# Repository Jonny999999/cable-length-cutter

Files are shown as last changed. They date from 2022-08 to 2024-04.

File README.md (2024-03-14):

# Overview
Firmware and documentation of a custom built machine that winds and cuts cable to certain lengths.  
Extensive details about this project can be found on the website: [pfusch.zone/cable-length-cutter](https://pfusch.zone/cable-length-cutter)

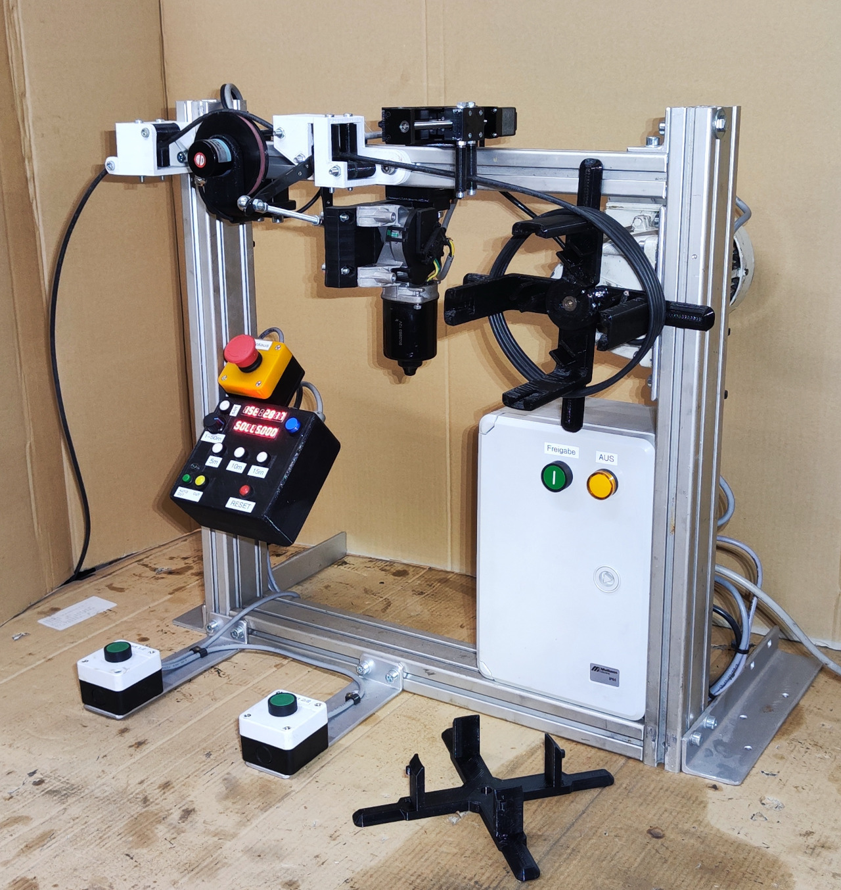
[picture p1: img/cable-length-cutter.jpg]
Photo machine


Photo of the built machine

## Current Features
- Measure length using rotary encoder
- Wind to set length while start-button is pressed
- Automatic wire cutter
- Control interface:
  - 2x 7-Segment display showing lengths and notifications
  - Buzzer for acoustic notifications
  - 4 Buttons and Potentiometer for setting the target length
  - Reset and Cut Button
- Stepper motor controlling a linear axis guiding the cable while winding
- Store last axis position at shutdown

# Usage
Panel Layout

# Electrical Details
For detailed documentation of all electrical aspects, see [connection-plan.pdf](connection-plan.pdf).

# Printed Parts
All designed and 3D-printed parts can be found in the [cad/](cad/) folder. These parts were designed using FreeCAD.

# Components
### Custom pcb with ESP-32 microcontroller
See [connection-plan.pdf](connection-plan.pdf)  

### Rotary encoder LPD3806-600BM-G5-24C
```
- Pulses: 600 p/r (Single-phase 600 pulses /R,Two phase 4 frequency doubling to 2400 pulses)
- Power source: DC5-24V
- Shaft: 6*13mm/0.23*0.51"
- Size: 38*35.5mm/1.49*1.39"
- Output :AB 2phase output rectangular orthogonal pulse circuit, the output for the NPN open collector output type
- Maximum mechanical speed: 5000 R / min
- Response frequency: 0-20KHz
- Cable length: 1.5 meter
- size: http://domoticx.com/wp-content/uploads/2020/05/LPD3806-afmetingen.jpg
- Wires: Green = A phase, white = B phase, red = Vcc power +, black = V0
```
### Variable Frequency Drive T13-400W-12-H
See [docs/vfd/](docs/vfd/)

### Stepper-driver TB6600
See [docs/stepper-driver_TB6600-Manual.pdf](docs/stepper-driver_TB6600-Manual.pdf)

### Linear Axis with Nema-12 28HB40 Stepper
See [connection-plan.pdf](connection-plan.pdf)  

# Installation
For this project **ESP-IDF v4.4.4** is required (with other versions it might not compile)
```bash
#download esp-idf
yay -S esp-idf 
#alternatively clone the esp-idf repository from github and do `git checkout release/4.4`

#run installation script in installed folder
/opt/esp-idf/install.sh
```

# Build
### Set up environment
```bash
source /opt/esp-idf/export.sh
```
(run once per terminal)

### Compile
```bash
cd board_single
idf.py build
```

# Flash
- connect FTDI programmer to board (VCC to VCC; TX to RX; RX to TX)
- press REST and BOOT button
- release RESET button (keep pressing boot)
- run flash command:
```bash
idf.py flash
```

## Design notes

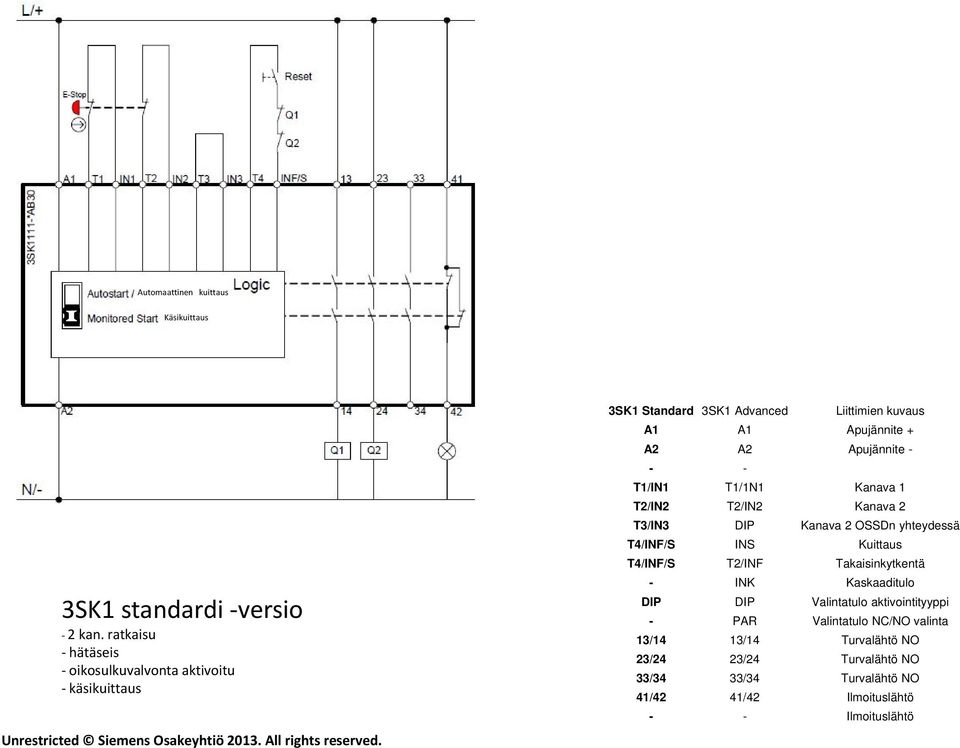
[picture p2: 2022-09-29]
docs/safety-relay_3SK1111-1AB30_con1.jpg

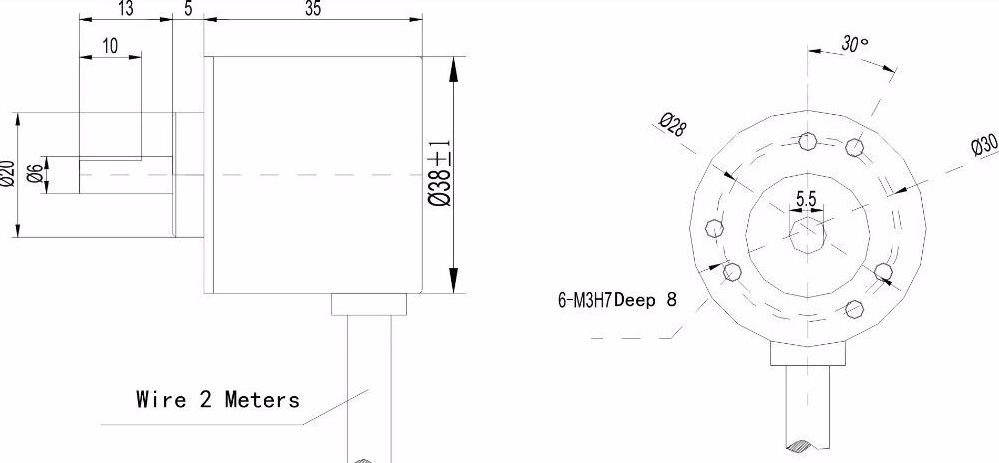
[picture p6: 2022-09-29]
docs/encoder-LPD3806_dimensions.jpg

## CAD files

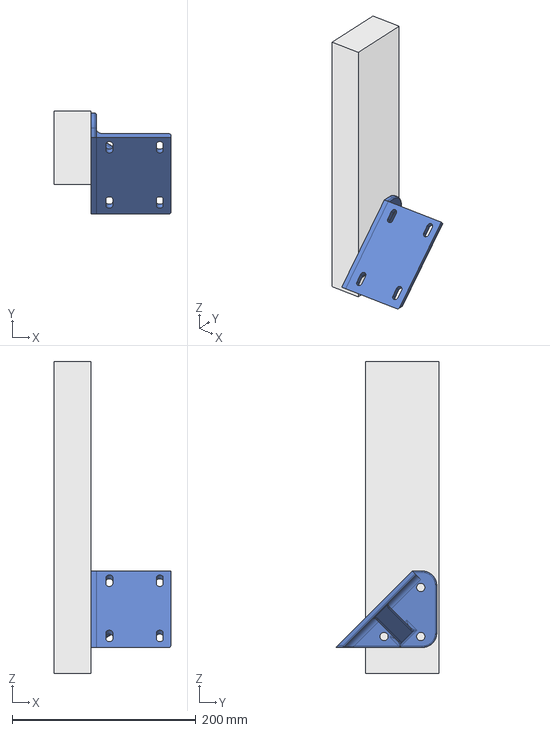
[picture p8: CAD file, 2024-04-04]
cad/box/box-holder_v1.0.FCStd
127.1 x 112.5 x 340.0 mm
item
ADAPTER

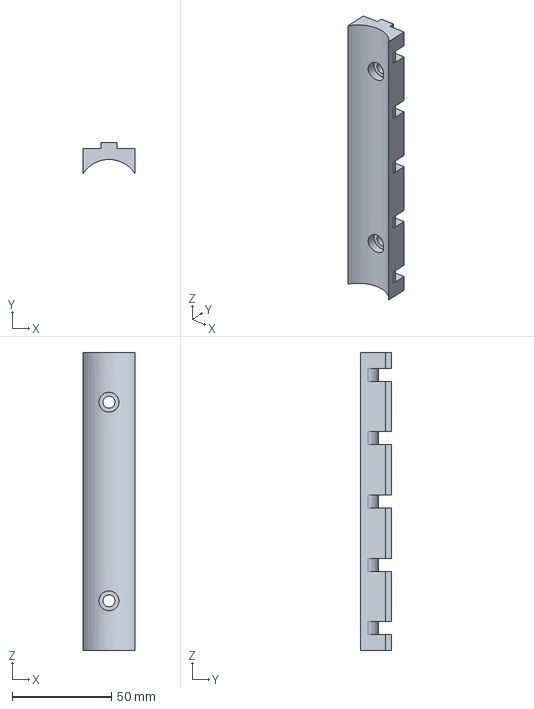
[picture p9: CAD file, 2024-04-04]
cad/cable-mounts/mounts-item.FCStd
26.0 x 15.5 x 150.0 mm

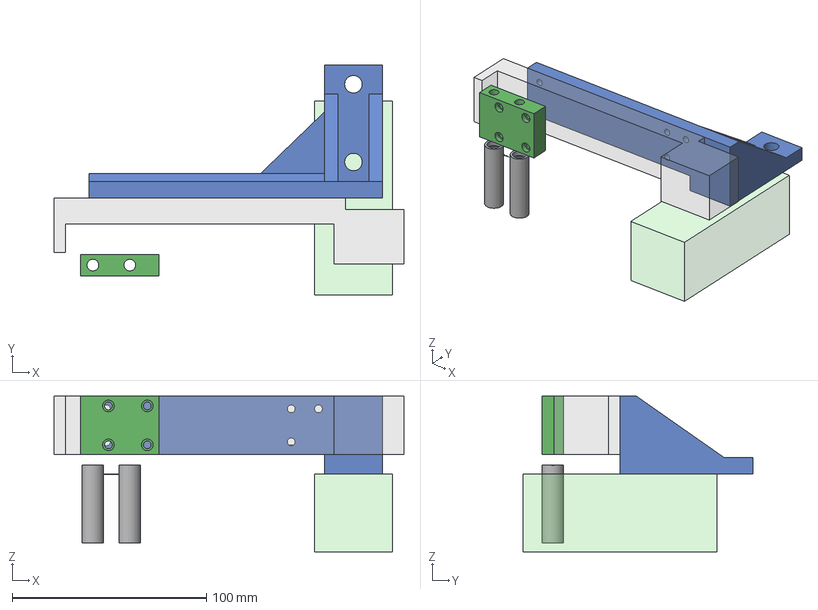
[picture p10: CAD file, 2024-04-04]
cad/cnc-guide/axis_mounts.FCStd
180.0 x 118.5 x 80.0 mm
roll

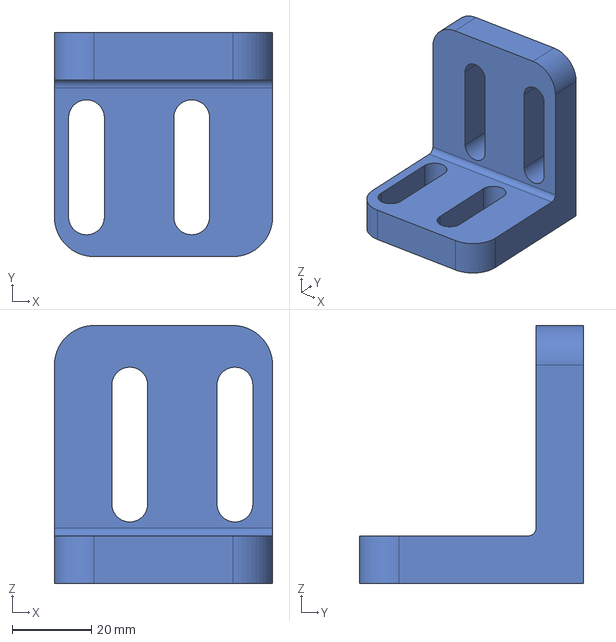
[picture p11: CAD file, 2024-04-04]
cad/cutter/angle-bracket_v2.0.FCStd
55.0 x 56.5 x 65.0 mm

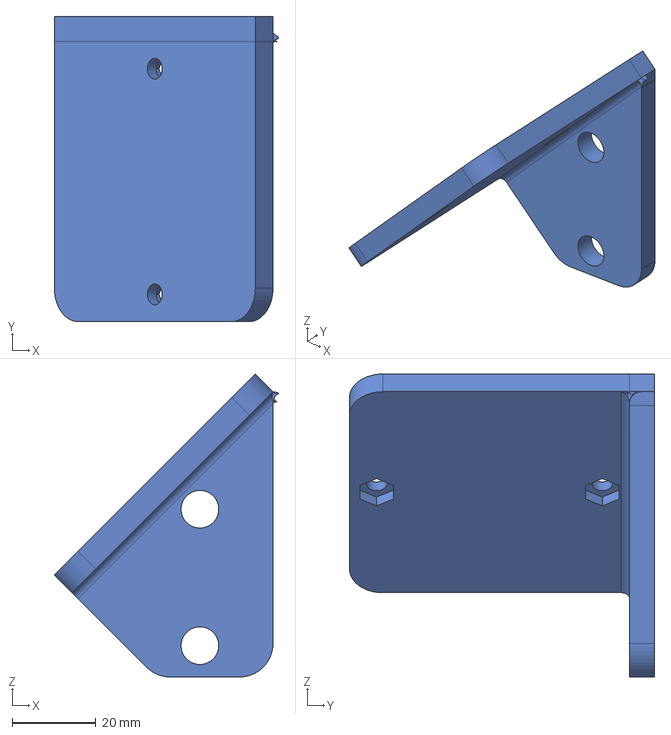
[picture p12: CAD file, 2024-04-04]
cad/emergency-sw/sw_holder_v1.0.FCStd
53.7 x 73.0 x 72.5 mm

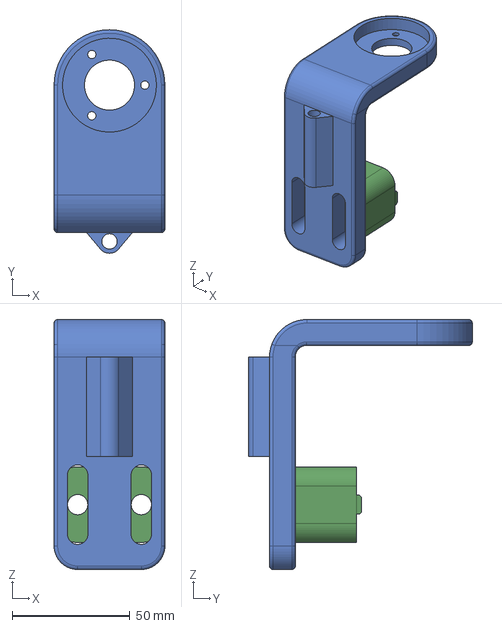
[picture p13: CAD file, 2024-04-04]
cad/encoder/holder_v3.2.FCStd
47.0 x 94.8 x 106.0 mm
bracket

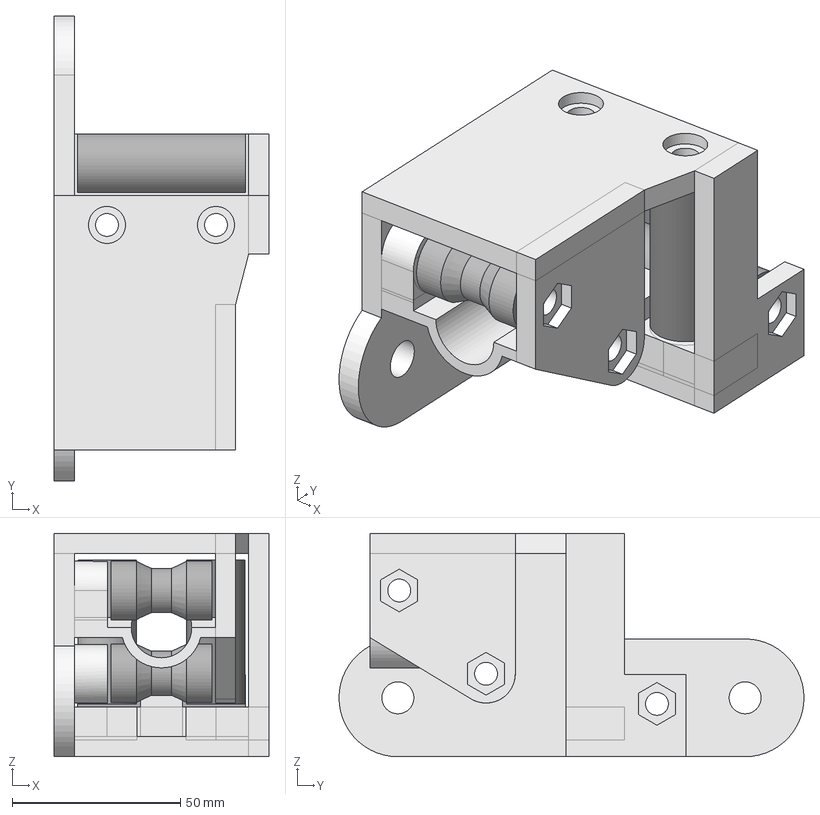
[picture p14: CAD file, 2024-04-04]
cad/guides/guide-cutter_v5.1.FCStd
63.8 x 138.2 x 66.4 mm
roll_top_beforeCutter
roll_bot
rolls_vertical
roll_bot_beforeCutter
rolls_vertical (Mirror #1)
main-walls

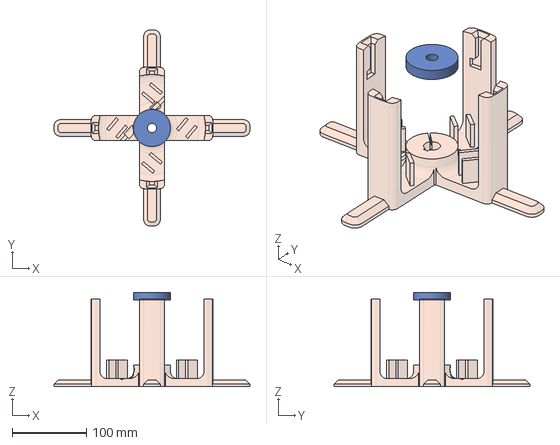
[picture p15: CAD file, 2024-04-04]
cad/reel/cable-reel_v2.2.2.FCStd
264.0 x 264.0 x 127.0 mm
REEL
center

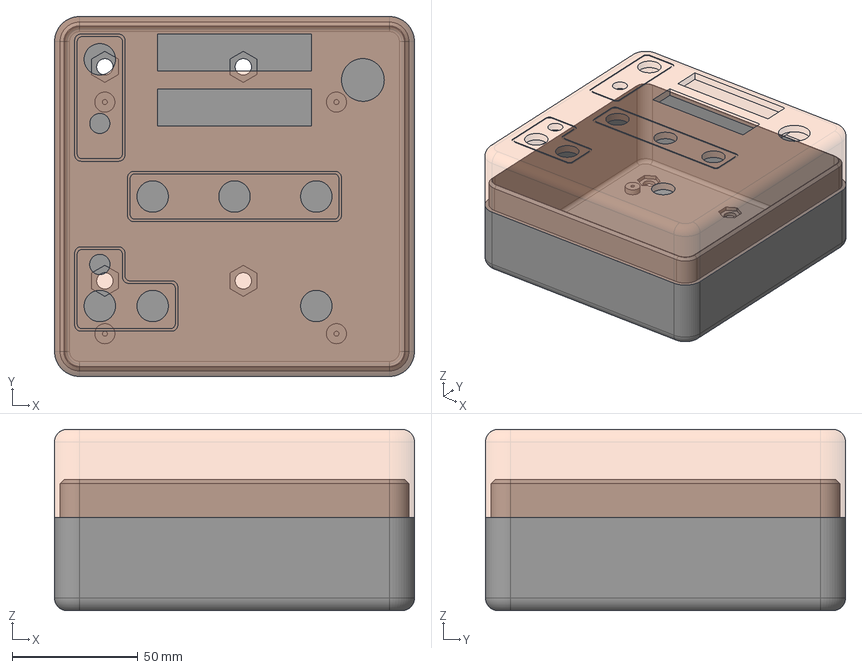
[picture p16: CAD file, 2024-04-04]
cad/box/box_v1.0.FCStd
143.0 x 143.0 x 72.0 mm
TOP
BOT

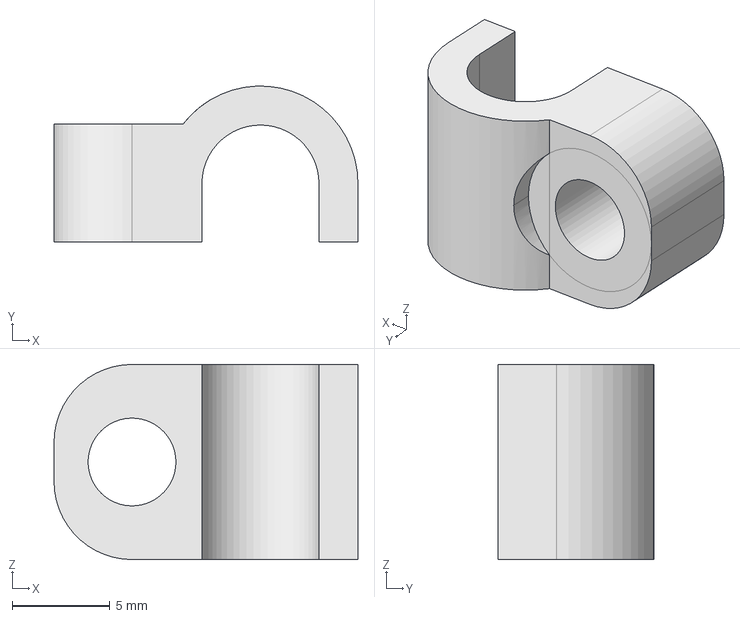
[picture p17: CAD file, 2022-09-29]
cad/cable-mounts/clamps-startButtons.FCStd
15.6 x 7.99 x 10.0 mm

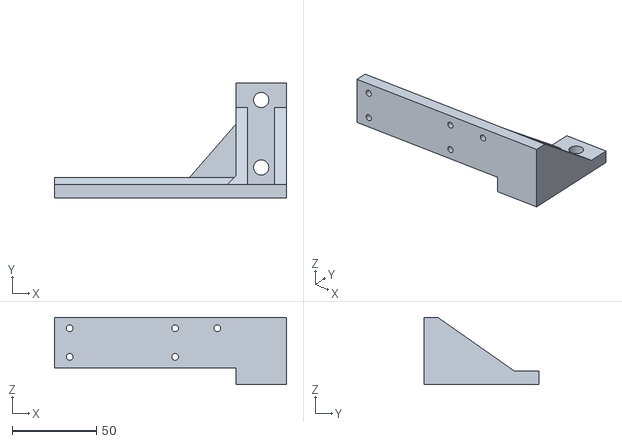
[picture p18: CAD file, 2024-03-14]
cad/cnc-guide/axis-mount.stl
137.5 x 68.0 x 40.0

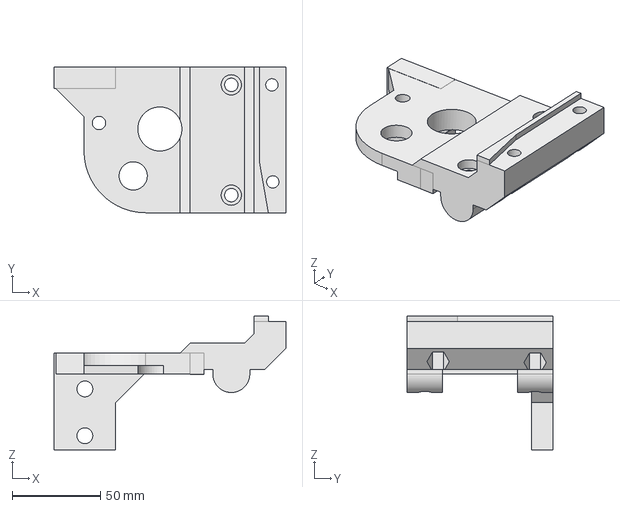
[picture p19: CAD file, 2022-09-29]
cad/cutter/cutter-mount_2.2.FCStd
131.5 x 82.5 x 75.8 mm

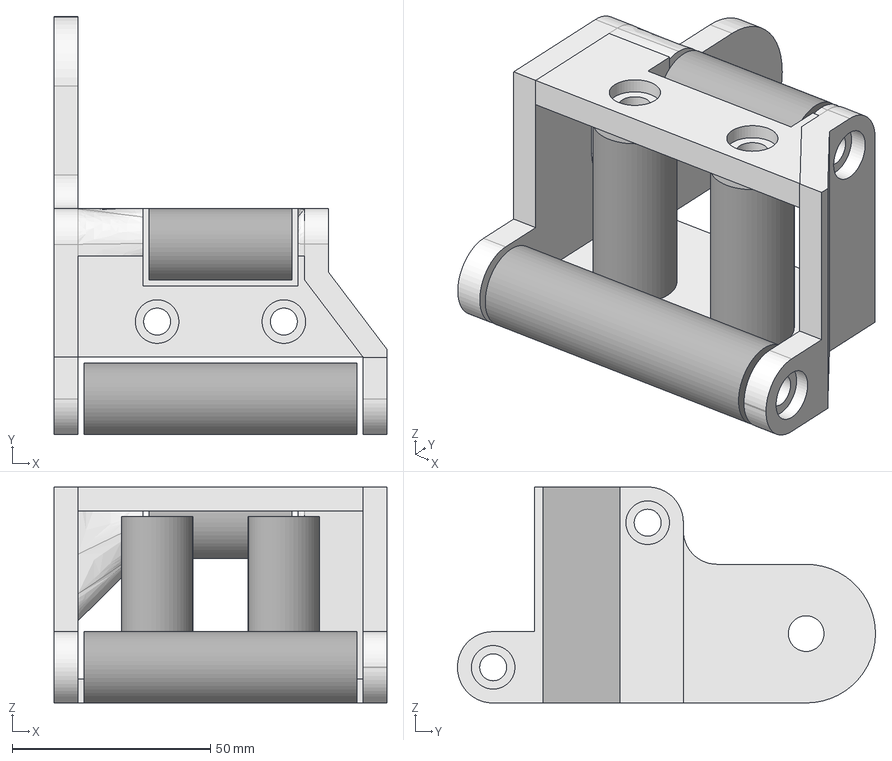
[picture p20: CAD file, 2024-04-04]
cad/guides/guide-in_v2.1.FCStd
84.0 x 105.5 x 54.5 mm
roll-bot
roll_vert
roll_vert (Mirror #1)
roll-top
rear-wall
front-wall
top-wall
bot-wall

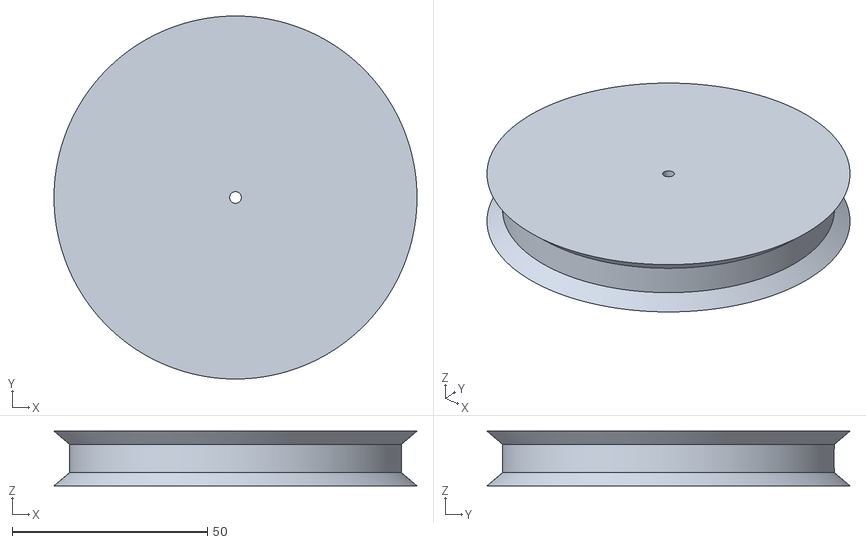
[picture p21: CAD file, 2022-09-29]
cad/encoder/disk-flat_SE.stl
93.0 x 93.0 x 14.0

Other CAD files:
cad/assembly_all-parts.FCStd
cad/guides/guide-cutter_spacer.FCStd
cad/guides/guide-in-long_SE.stl
cad/guides/distance-rings.FCStd
cad/encoder/holder_v1.0.FCStd
cad/encoder/holder_v2.0.FCStd
cad/guides/guide-cutter_v1.0.FCStd
cad/guides/guide-cutter_v2.0.FCStd
cad/guides/guide-cutter_v3.0.FCStd
cad/guides/guide-cutter_v4.2.FCStd
cad/guides/guide-cutter_v5.0.FCStd
cad/guides/guide-in-long-rolls_SE.stl
cad/guides/guide-in_v1.0.FCStd
cad/guides/guide-in_v1.1.FCStd
cad/reel/cable-reel_v2.1.FCStd
cad/reel/cable-reel_v2.2.FCStd

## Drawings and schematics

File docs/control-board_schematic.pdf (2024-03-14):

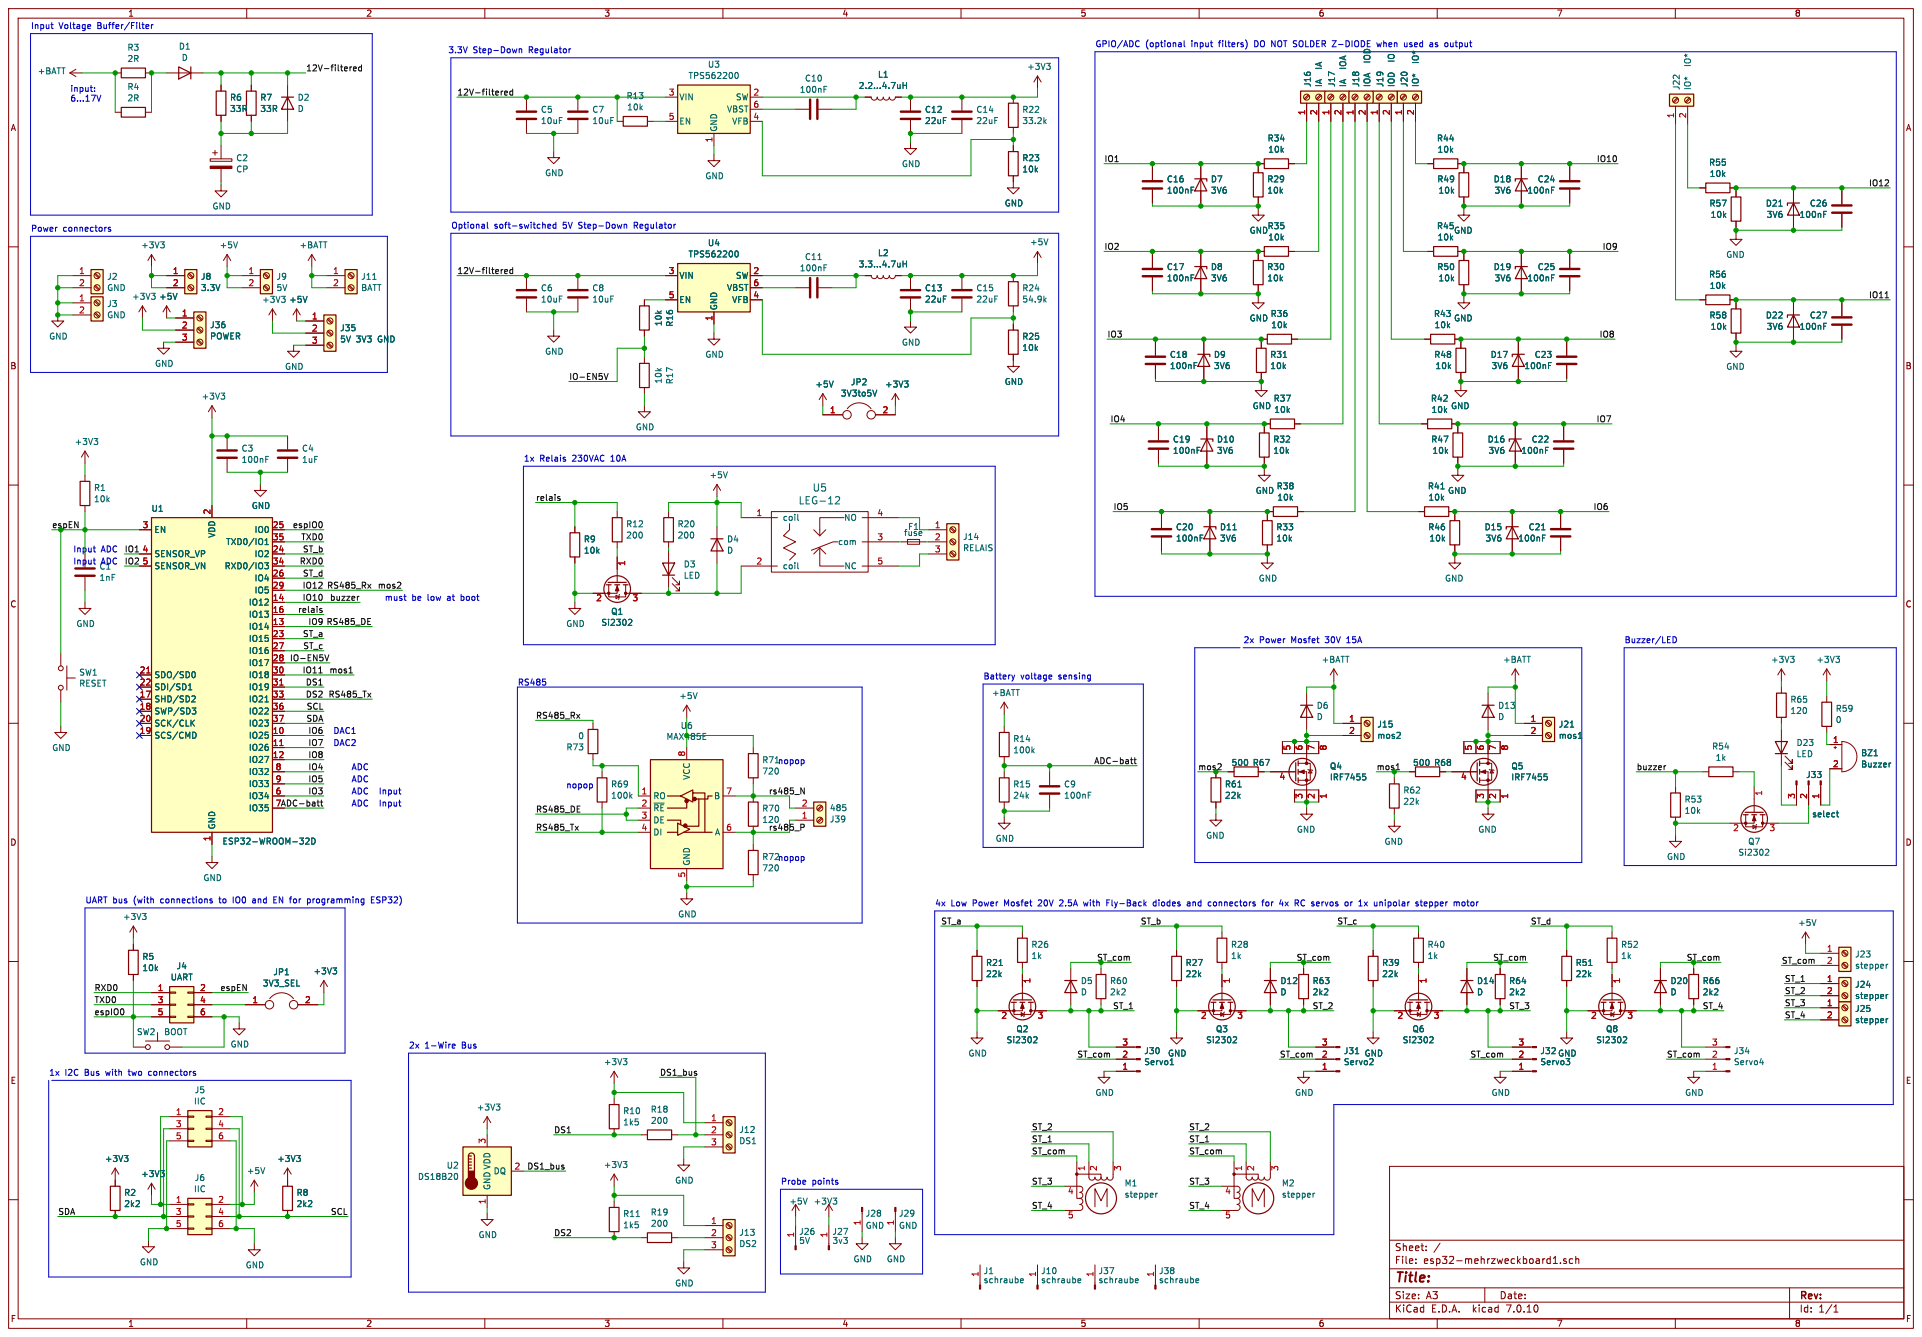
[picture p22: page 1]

Input Voltage Buffer/Filter ADC

1 SW 2 VIN 3 VFB 4 EN 5 VBST 6 U3 TPS562200 GND

1 SW 2 VIN 3 VFB 4 EN 5 VBST 6 U4 TPS562200 R72

1 SW 2 VIN 3 VFB 4 EN 5 VBST 6 GND

2 SCK/CLK 20 SDO/SD0 21 SDI/SD1 22

Id: 1/1 Title: File: esp32-mehrzweckboard1.sch Sheet: /

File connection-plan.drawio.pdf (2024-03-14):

# Connection plan - cable length cutter

### 12V Relay-COM (cutter)

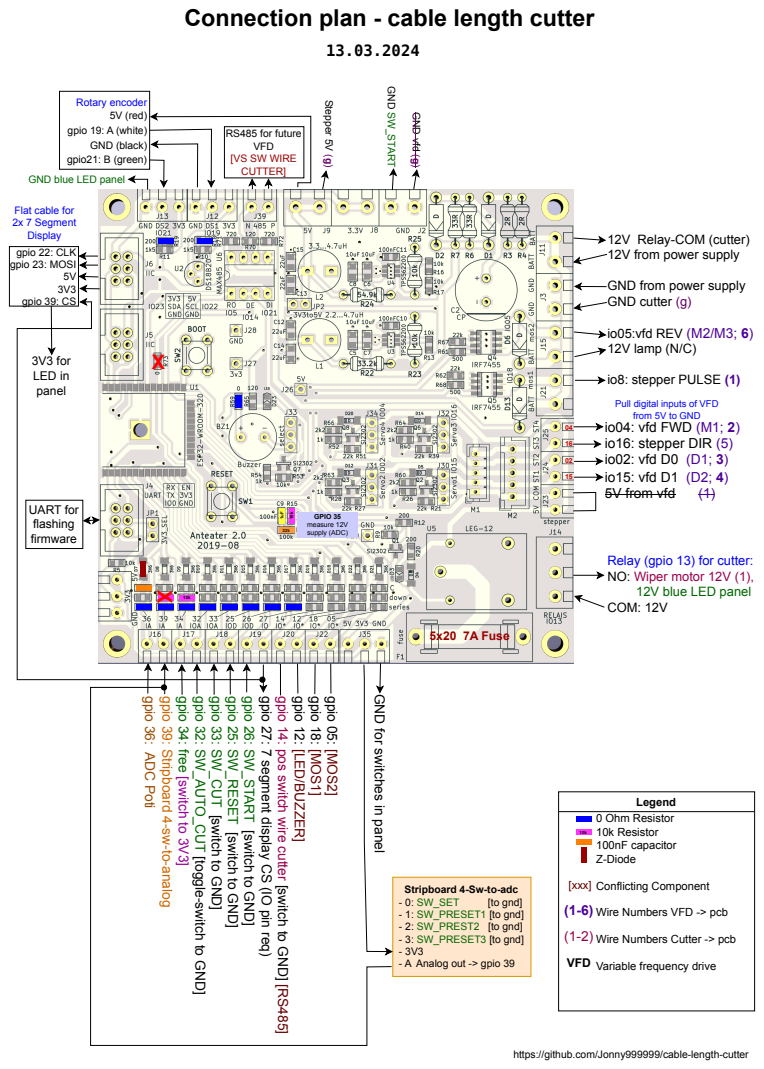
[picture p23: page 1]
gpio 05: [MOS2]; gpio 18: [MOS1]; gpio 26: SW_STAR; gpio 36:; ADC Poti; 5V from vfd; Legend 0 Ohm Resistor 10k Resistor 100nF capacitor Z-Diode; io05:vfd REV (M2/M3; 6) 12V lamp (N/C); io8: stepper PULSE (1); 5V 3V3 gpio 39: CS; UART for flashing firmware; Rotary encoder 5V (red) gpio 19: A (white) GND (black) gpio21: B (green); - 0: SW_SET; [to gnd]; GND vfd (g); GND SW_STAR; Stepper 5V (g); 5x20 7A Fuse; 3V3 for LED in panel; GPIO 35 measure 12V supply (ADC)

RS485 for future
VFD
[VS SW WIRE
CUTTER]

GND blue LED panel

Flat cable for
2x 7 Segment
Display
gpio 22: CLK
gpio 23: MOSI

12V from power supply

GND from power supply
GND cutter (g)

Pull digital inputs of VFD
from 5V to GND
io04: vfd FWD (M1; 2)
io16: stepper DIR (5)
io02: vfd D0 (D1; 3)
io15: vfd D1 (D2; 4)

Relay (gpio 13) for cutter:
NO: Wiper motor 12V (1),
12V blue LED panel
COM: 12V

gpio 39: Stripboard 4-sw-to-analog

gpio 34: free [switch to 3V3]

gpio 32: SW_AUTO_CUT [toggle-switch to GND]

gpio 33: SW_CUT [switch to GND]

gpio 25: SW_RESET [switch to GND]

gpio 27: 7 segment display CS (IO pin req)

gpio 14: pos switch wire cutter [switch to GND] [RS485]

gpio 12: [LED/BUZZER]

GND for switches in panel

T [switch to GND]

Stripboard 4-Sw-to-adc
- 1: SW_PRESET1 [to gnd]
- 2: SW_PREST2 [to gnd]
- 3: SW_PRESET3 [to gnd]
- A Analog out -> gpio 39

[xxx]
Conflicting Component
Wire Numbers VFD -> pcb
Wire Numbers Cutter -> pcb
Variable frequency drive

https://github.com/Jonny999999/cable-length-cutter

## Control panel layout

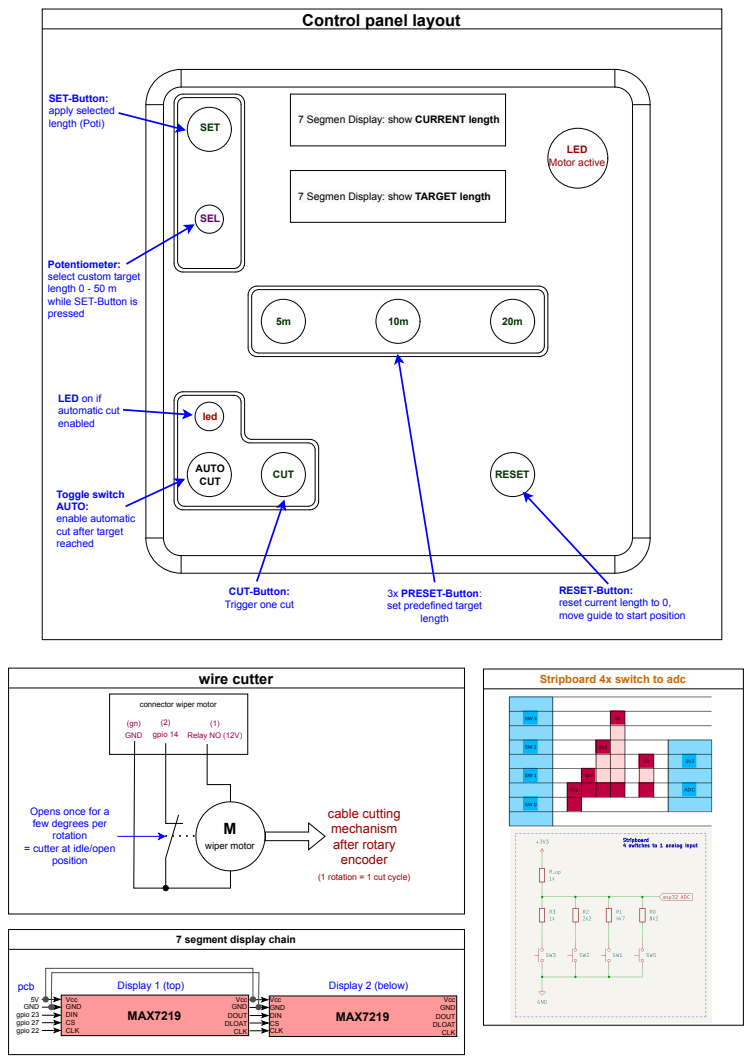
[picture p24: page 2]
MAX7219; Vcc GND DIN CS CLK; 5V GND gpio 23 gpio 27 gpio 22; Vcc GND DOUT DLOAT CLK; pcb; Display 1 (top); Display 2 (below); wire cutter; wiper motor; (2) gpio 14; (gn) GND; (1) Relay NO (12V); cable cutting mechanism after rotary encoder; CUT; RESET AUTO; SEL; SET; LED Motor active; SET-Button: apply selected length (Poti); led

7 Segmen Display: show CURRENT length

7 Segmen Display: show TARGET length

Potentiometer:
select custom target
length 0 - 50 m
while SET-Button is
pressed

LED on if
automatic cut
enabled

Toggle switch
AUTO:
enable automatic
cut after target
reached

CUT-Button:
Trigger one cut

3x PRESET-Button:
set predefined target
length

RESET-Button:
reset current length to 0,
move guide to start position

Stripboard 4x switch to adc

connector wiper motor

Opens once for a
few degrees per
rotation
= cutter at idle/open
position

(1 rotation = 1 cut cycle)

7 segment display chain

## Stepper driver

1 1 1 0 1 0

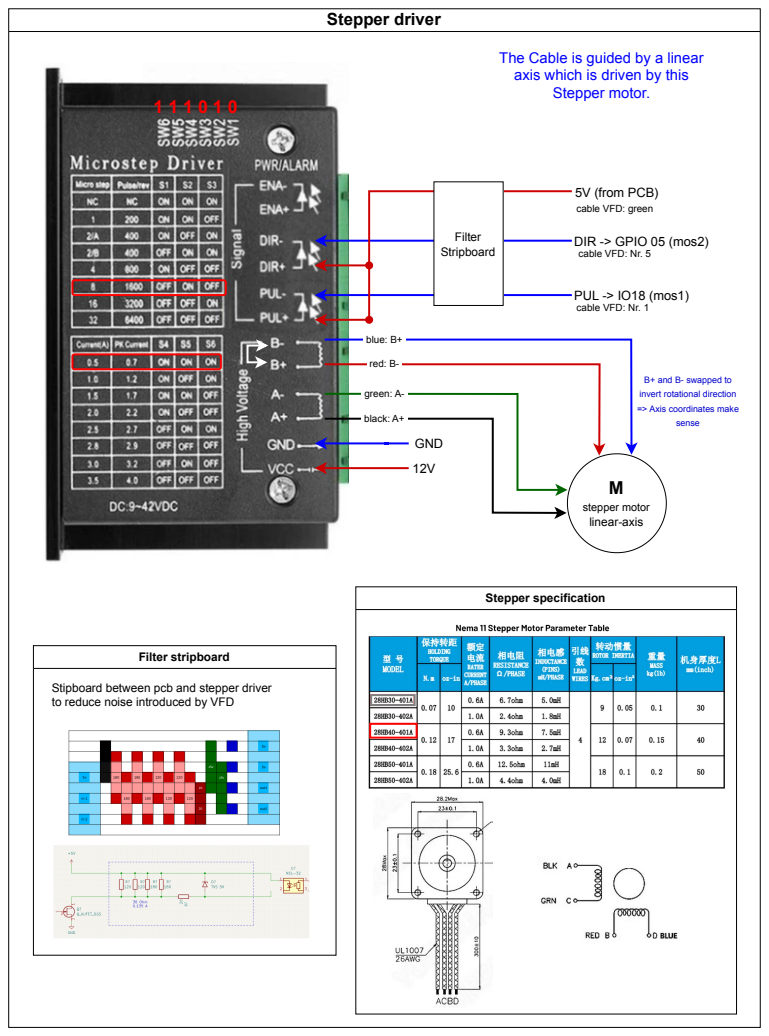
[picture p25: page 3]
stepper motor linear-axis; GND; green: A-; black: A+; blue: B+; red: B-; sense; Filter stripboard; Stepper specification

The Cable is guided by a linear
axis which is driven by this
Stepper motor.

5V (from PCB)
cable VFD: green

Filter
Stripboard

DIR -> GPIO 05 (mos2)
cable VFD: Nr. 5

PUL -> IO18 (mos1)
cable VFD: Nr. 1

B+ and B- swapped to
invert rotational direction
=> Axis coordinates make

Stipboard between pcb and stepper driver
to reduce noise introduced by VFD

## Wiring-plan

## Motor

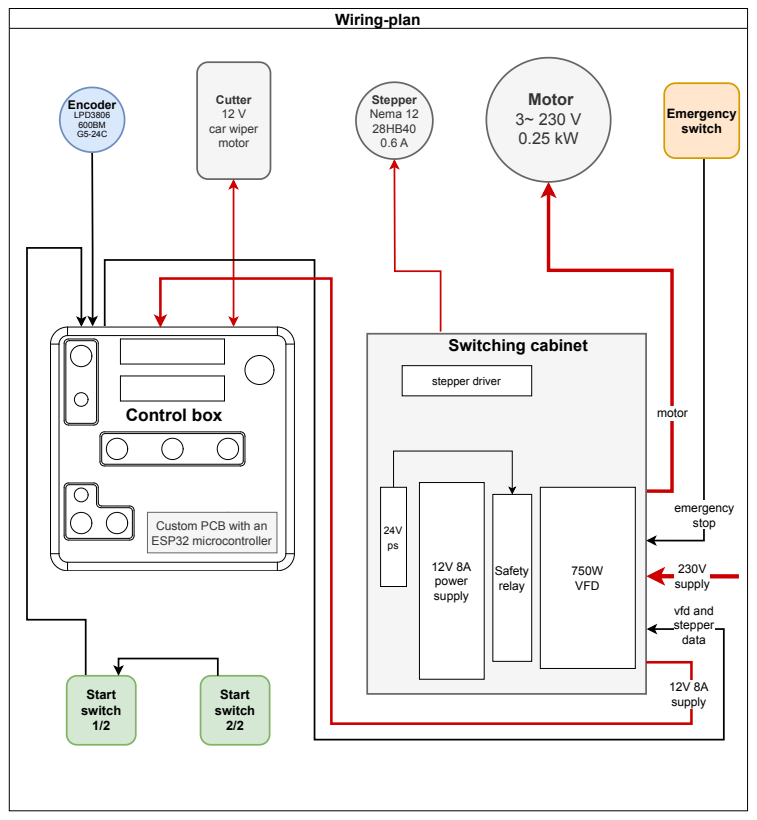
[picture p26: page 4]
Encoder LPD3806 600BM G5-24C; Cutter 12 V car wiper motor; motor; vfd and stepper data; 12V 8A supply; 12V 8A power supply; Safety relay; 750W VFD; Start switch 1/2; Start switch 2/2; emergency stop; Emergency switch; 230V supply; Switching cabinet; Control box; Stepper Nema 12 28HB40 0.6 A; stepper driver

Custom PCB with an
ESP32 microcontroller

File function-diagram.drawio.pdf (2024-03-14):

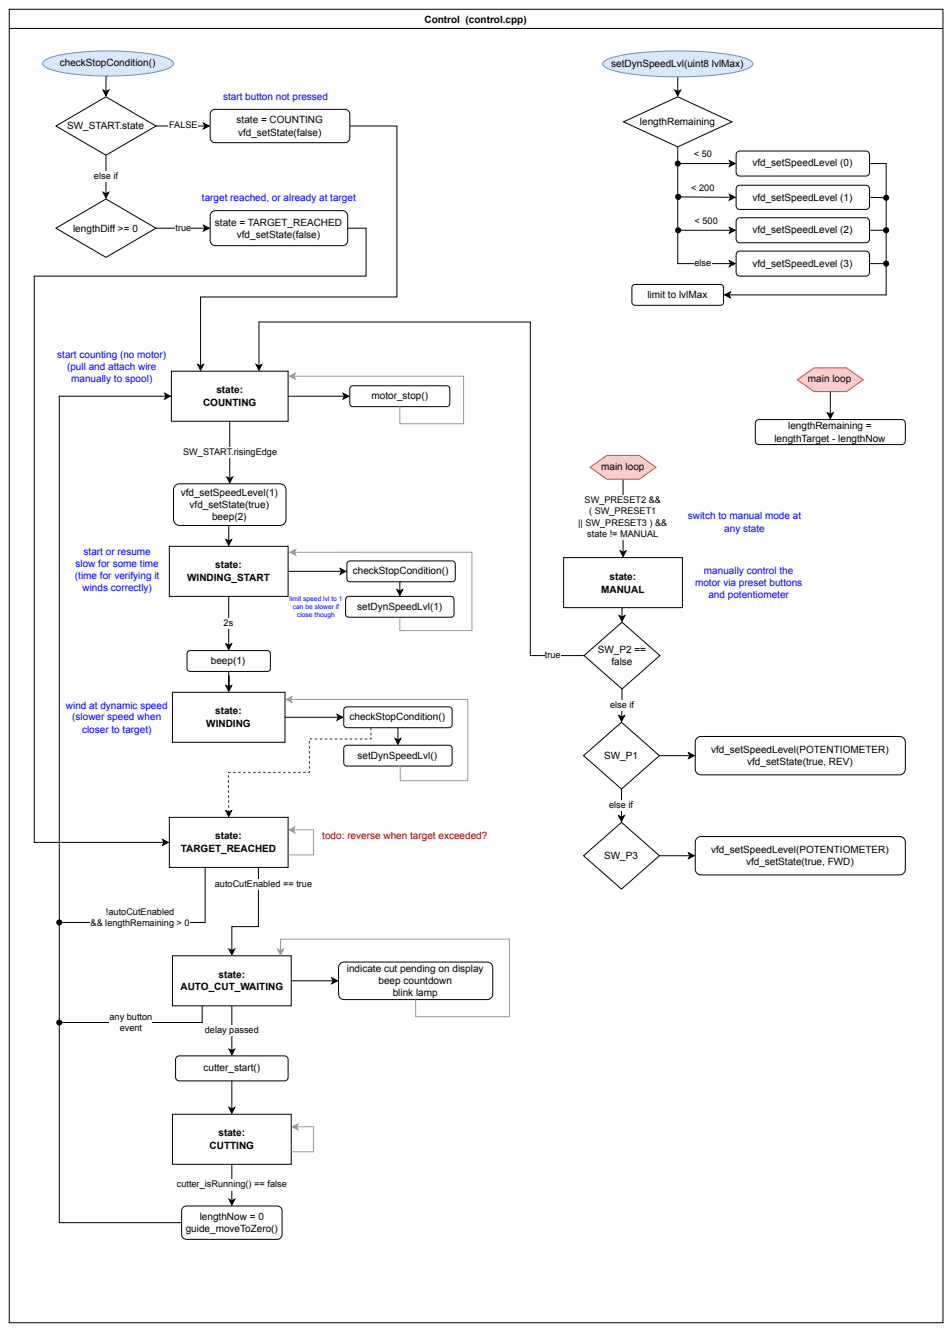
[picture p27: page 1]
state: WINDING_START; state: WINDING; !autoCutEnabled && lengthRemaining > 0; autoCutEnabled == true; state: TARGET_REACHED; SW_PRESET2 && ( SW_PRESET1 || SW_PRESET3 ) && state != MANUAL; state: COUNTING; vfd_setSpeedLevel(1) vfd_setState(true) beep(2); SW_START.risingEdge; beep(1); lengthDiff >= 0; true; state = TARGET_REACHED; vfd_setState(false); else if; SW_START.state; state = COUNTING; FALSE; state: MANUAL; motor_stop(); vfd_setSpeedLevel(POTENTIOMETER) vfd_setState(true, REV)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

Control (control.cpp)

start button not pressed

target reached, or already at target

limit to lvlMax

start counting (no motor)
(pull and attach wire
manually to spool)

switch to manual mode at

start or resume
slow for some time
(time for verifying it
winds correctly)

manually control the
motor via preset buttons
and potentiometer

limit speed lvl to 1
can be slower if
close though

wind at dynamic speed
(slower speed when
closer to target)

todo: reverse when target exceeded?

indicate cut pending on display
beep countdown
blink lamp

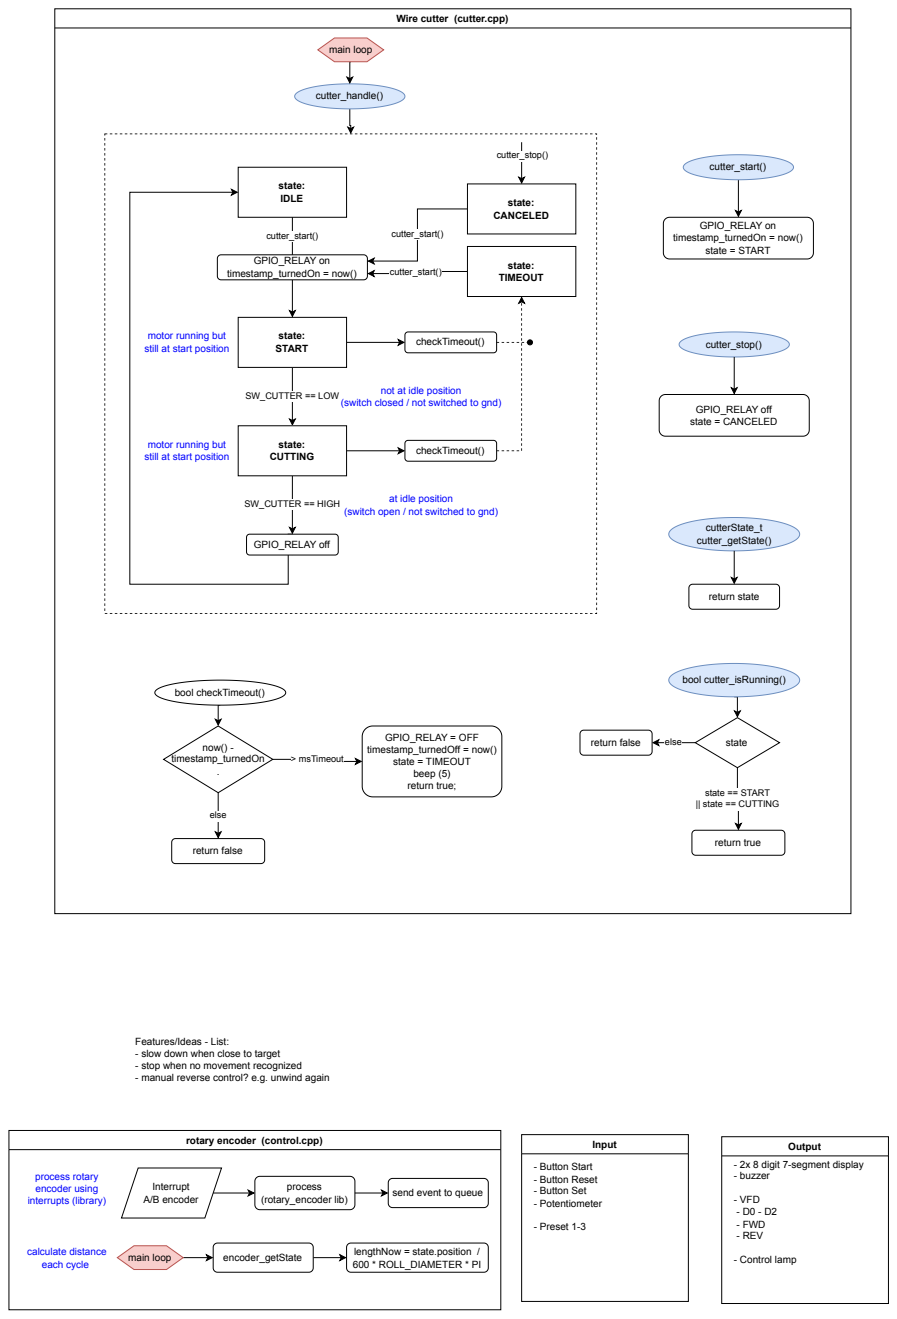
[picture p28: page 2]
Input; - Button Start - Button Reset - Button Set - Potentiometer; - Preset 1-3; Output; - VFD - D0 - D2 - FWD - REV; - Control lamp; Interrupt A/B encoder; process; (rotary_encoder lib); send event to queue; process rotary encoder using interrupts (library); encoder_getState; lengthNow = state.position /; 600 * ROLL_DIAMETER * PI; calculate distance; each cycle; main loop; SW_CUTTER == LOW; state: IDLE; SW_CUTTER == HIGH; state: CUTTING; state: START; GPIO_RELAY on timestamp_turnedOn = now()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

Wire cutter (cutter.cpp)

motor running but
still at start position

not at idle position

(switch closed / not switched to gnd)

at idle position

(switch open / not switched to gnd)

Features/Ideas - List:
- slow down when close to target
- stop when no movement recognized
- manual reverse control? e.g. unwind again

rotary encoder (control.cpp)

- 2x 8 digit 7-segment display
- buzzer

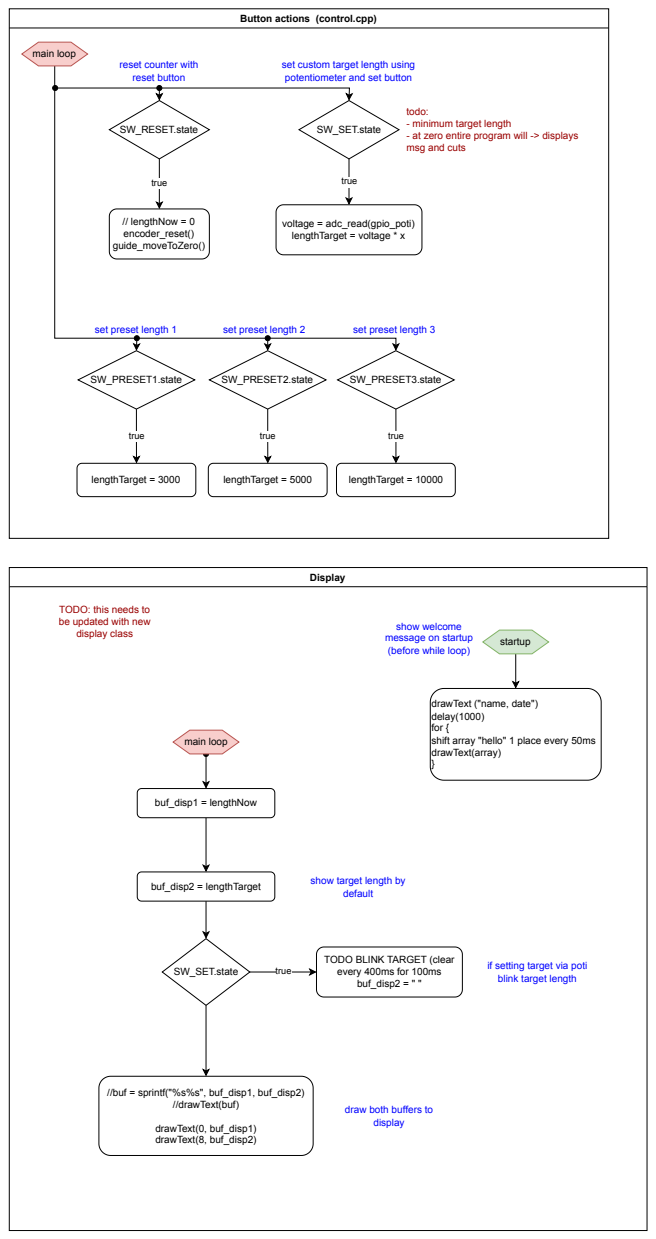
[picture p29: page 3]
SW_RESET.state; // lengthNow = 0 encoder_reset() guide_moveToZero(); true; SW_SET.state; voltage = adc_read(gpio_poti) lengthTarget = voltage * x; SW_PRESET1.state; lengthTarget = 3000; SW_PRESET2.state; lengthTarget = 5000; SW_PRESET3.state; lengthTarget = 10000; main loop; Display; buf_disp2 = lengthTarget; show target length by; default; buf_disp1 = lengthNow; //buf = sprintf("%s%s", buf_disp1, buf_disp2) //drawText(buf); drawText(0, buf_disp1) drawText(8, buf_disp2); startup

Button actions (control.cpp)

reset counter with
reset button

set custom target length using
potentiometer and set button

todo:
- minimum target length
- at zero entire program will -> displays
msg and cuts

set preset length 1

set preset length 2

set preset length 3

TODO: this needs to
be updated with new
display class

show welcome
message on startup
(before while loop)

drawText ("name, date")
delay(1000)
for {
shift array "hello" 1 place every 50ms
drawText(array)

TODO BLINK TARGET (clear
every 400ms for 100ms
buf_disp2 = " "

if setting target via poti
blink target length

draw both buffers to
display

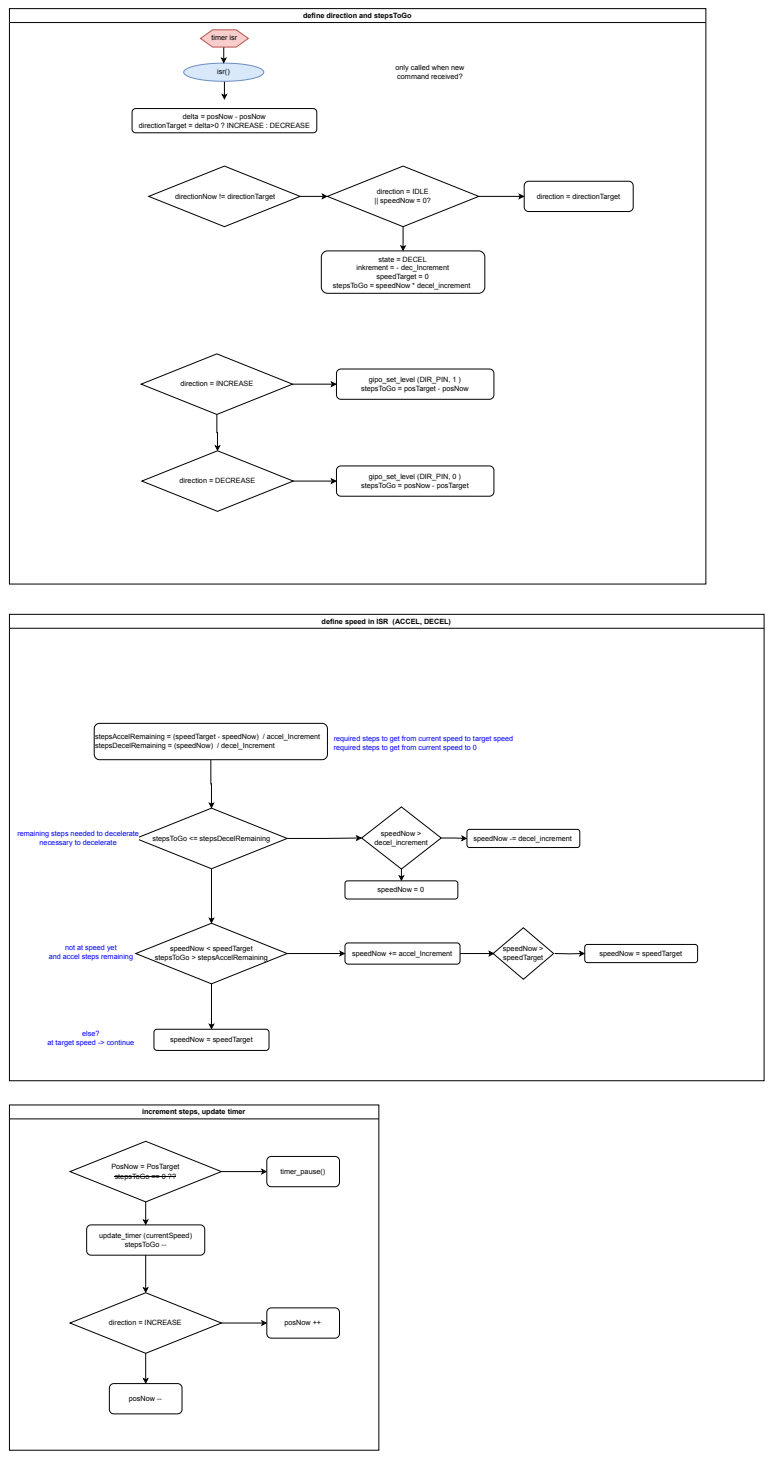
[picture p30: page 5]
isr(); timer isr; directionNow != directionTarget; state = DECEL inkrement = - dec_Increment speedTarget = 0 stepsToGo = speedNow * decel_increment; direction = INCREASE; direction = directionTarget; direction = DECREASE; gipo_set_level (DIR_PIN, 0 ); direction = IDLE || speedNow = 0?; speedNow < speedTarget stepsToGo > stepsAccelRemaining; stepsToGo <= stepsDecelRemaining; speedNow += accel_Increment; speedNow = speedTarget; else?; speedNow > decel_increment; speedNow = 0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

define direction and stepsToGo

only called when new
command received?

delta = posNow - posNow

directionTarget = delta>0 ? INCREASE : DECREASE

gipo_set_level (DIR_PIN, 1 )
stepsToGo = posTarget - posNow

stepsToGo = posNow - posTarget

define speed in ISR (ACCEL, DECEL)

stepsAccelRemaining = (speedTarget - speedNow) / accel_Increment
stepsDecelRemaining = (speedNow) / decel_Increment

required steps to get from current speed to target speed
required steps to get from current speed to 0

remaining steps needed to decelerate
necessary to decelerate

not at speed yet
and accel steps remaining

at target speed -> continue

increment steps, update timer

delta = po
stepsTo

speedTar

step

speedTar

ACCELERATING

DECELERATING

TARGET REACHED

COASTING / at speed | speedNow
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

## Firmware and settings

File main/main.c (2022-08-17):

#include <stdio.h>
#include <freertos/FreeRTOS.h>
#include <freertos/task.h>
#include <esp_idf_version.h>
#include "freertos/queue.h"
#include "esp_system.h"
#include "esp_log.h"

#include <max7219.h>
#include "rotary_encoder.h"

//--------------------------
//----- display config -----
//--------------------------
#if ESP_IDF_VERSION < ESP_IDF_VERSION_VAL(4, 0, 0)
#define HOST    HSPI_HOST
#else
#define HOST    SPI2_HOST
#endif
#define DISPLAY_PIN_NUM_MOSI 23
#define DISPLAY_PIN_NUM_CLK 18
#define DISPLAY_PIN_NUM_CS 21
#define DISPLAY_DELAY 2000

//--------------------------
//----- encoder config -----
//--------------------------
#define TAG "app"
#define ROT_ENC_A_GPIO 16
#define ROT_ENC_B_GPIO 17
#define ENABLE_HALF_STEPS false  // Set to true to enable tracking of rotary encoder at half step resolution
#define FLIP_DIRECTION    false  // Set to true to reverse the clockwise/counterclockwise sense

#define MEASURING_ROLL_DIAMETER 44
#define PI 3.14159265358979323846




void task(void *pvParameter)
{

    //========================
    //===== init encoder =====
    //========================
    // esp32-rotary-encoder requires that the GPIO ISR service is installed before calling rotary_encoder_register()
    ESP_ERROR_CHECK(gpio_install_isr_service(0));

    // Initialise the rotary encoder device with the GPIOs for A and B signals
    rotary_encoder_info_t info = { 0 };
    ESP_ERROR_CHECK(rotary_encoder_init(&info, ROT_ENC_A_GPIO, ROT_ENC_B_GPIO));
    ESP_ERROR_CHECK(rotary_encoder_enable_half_steps(&info, ENABLE_HALF_STEPS));
#ifdef FLIP_DIRECTION
    ESP_ERROR_CHECK(rotary_encoder_flip_direction(&info));
#endif

    // Create a queue for events from the rotary encoder driver.
    // Tasks can read from this queue to receive up to date position information.
    QueueHandle_t event_queue = rotary_encoder_create_queue();
    ESP_ERROR_CHECK(rotary_encoder_set_queue(&info, event_queue));




    //========================
    //===== init display =====
    //========================
    // Configure SPI bus
    spi_bus_config_t cfg = {
       .mosi_io_num = DISPLAY_PIN_NUM_MOSI,
       .miso_io_num = -1,
       .sclk_io_num = DISPLAY_PIN_NUM_CLK,
       .quadwp_io_num = -1,
       .quadhd_io_num = -1,
       .max_transfer_sz = 0,
       .flags = 0
    };
    ESP_ERROR_CHECK(spi_bus_initialize(HOST, &cfg, 1));

    // Configure device
    max7219_t dev = {
       .cascade_size = 1,
       .digits = 8,
       .mirrored = true
    };
    ESP_ERROR_CHECK(max7219_init_desc(&dev, HOST, MAX7219_MAX_CLOCK_SPEED_HZ, DISPLAY_PIN_NUM_CS));

    ESP_ERROR_CHECK(max7219_init(&dev));

    //0...15
    ESP_ERROR_CHECK(max7219_set_brightness(&dev, 12));



    char buf[10]; // 8 digits + decimal point + \0
    int32_t distance_mm = 0;

    //display startup message
        max7219_clear(&dev);
        max7219_draw_text_7seg(&dev, 0, "ABCDEFGH");
        printf("showing startup message...");
        vTaskDelay(pdMS_TO_TICKS(1000));


        //===== loop =====
        while (1)
        {


            vTaskDelay(pdMS_TO_TICKS(10)); //limit processing of events


            // Wait for incoming events on the event queue.
            rotary_encoder_event_t event = { 0 };
            if (xQueueReceive(event_queue, &event, 1000 / portTICK_PERIOD_MS) == pdTRUE)
            {
                ESP_LOGI(TAG, "Event: position %d, direction %s", event.state.position,
                        event.state.direction ? (event.state.direction == ROTARY_ENCODER_DIRECTION_CLOCKWISE ? "CW" : "CCW") : "NOT_SET");


                //--- calculate distalce ---
                distance_mm = event.state.position * (MEASURING_ROLL_DIAMETER * PI / 600); //TODO dont calculate constant factor every time
                //--- show current position on display ---
                //sprintf(buf, "%08d", event.state.position);
                //--- show current distance in cm on display ---
                sprintf(buf, "%06.1f cm", (float)distance_mm/10);
                //printf("float num\n");
                max7219_clear(&dev);
                max7219_draw_text_7seg(&dev, 0, buf);
            }
            else //no event for 1s
            {
                // Poll current position and direction
                rotary_encoder_state_t state = { 0 };
                ESP_ERROR_CHECK(rotary_encoder_get_state(&info, &state));
                ESP_LOGI(TAG, "Poll: position %d, direction %s", state.position,
                        state.direction ? (state.direction == ROTARY_ENCODER_DIRECTION_CLOCKWISE ? "CW" : "CCW") : "NOT_SET");

            }
        }
}






//display test
    //float count = 0;

//        printf("Display cycle\n");
//
//        max7219_clear(&dev);
//        max7219_draw_text_7seg(&dev, 0, "12345678");
//        printf("num");
//        vTaskDelay(pdMS_TO_TICKS(DISPLAY_DELAY));
//
//        max7219_clear(&dev);
//        max7219_draw_text_7seg(&dev, 0, "ABCDEFGH");
//        printf("text");
//        vTaskDelay(pdMS_TO_TICKS(DISPLAY_DELAY));
//
//
//        if (count > 20){
//            count = 0;
//        } else {
//            count += 0.005;
//        }
//
//        sprintf(buf, "%06.3f m", count);
//        //printf("float num\n");
//        max7219_clear(&dev);
//        max7219_draw_text_7seg(&dev, 0, buf);
//        vTaskDelay(pdMS_TO_TICKS(10));
//
   //     max7219_clear(&dev);
   //     sprintf(buf, "%08x", 12345678);
   //     printf("num\n");
   //     max7219_draw_text_7seg(&dev, 0, buf);
   //     vTaskDelay(pdMS_TO_TICKS(DISPLAY_DELAY));


//    }
//}

void app_main()
{
    xTaskCreate(task, "task", configMINIMAL_STACK_SIZE * 3, NULL, 5, NULL);
}

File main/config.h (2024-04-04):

#pragma once

#include "esp_idf_version.h"

//note: global variables and objects were moved to global.hpp

//===================================
//===== define output gpio pins =====
//===================================
//4x stepper mosfet outputs for VFD
#define GPIO_VFD_FWD GPIO_NUM_4     //ST4
#define GPIO_VFD_REV GPIO_NUM_5     //mos2
#define GPIO_VFD_D0 GPIO_NUM_2      //ST2
#define GPIO_VFD_D1 GPIO_NUM_15     //ST1
//#define GPIO_VFD_D2 GPIO_NUM_15     //ST1 (D2 only used with 7.5kw vfd)

#define GPIO_MOS1 GPIO_NUM_18       //mos1 (free) 2022.02.28: pin used for stepper
#define GPIO_LAMP GPIO_NUM_0        //mos2 (5) 2022.02.28: lamp disabled, pin used for stepper
#define GPIO_RELAY GPIO_NUM_13
#define GPIO_BUZZER GPIO_NUM_12


//==================================
//==== define analog input pins ====
//==================================
#define GPIO_POTI GPIO_NUM_36
#define ADC_CHANNEL_POTI ADC1_CHANNEL_0
#define GPIO_4SW_TO_ANALOG GPIO_NUM_39
#define ADC_CHANNEL_4SW_TO_ANALOG ADC1_CHANNEL_3 //gpio 39

#define ADC_CHANNEL ADC_CHANNEL_0
//#define ADC_LOW_VOLTAGE_THRESHOLD 1000 //adc value where shut down is detected (store certain values before power loss)
#define GPIO_PIN GPIO_NUM_2

#define ADC_CHANNEL_SUPPLY_VOLTAGE ADC1_CHANNEL_7//gpio35 onboard supply voltage
//ADC1_CHANNEL_0 gpio36
//ADC1_CHANNEL_6 gpio_34
//ADC1_CHANNEL_3 gpio_39


//=====================================
//==== assign switches to objects =====
//=====================================
//see config.cpp for available evaluated switch objects
#define SW_START sw_gpio_26
#define SW_RESET sw_gpio_25
#define SW_CUTTER_POS sw_gpio_14
#define SW_SET     sw_gpio_analog_0
#define SW_PRESET1 sw_gpio_analog_1
#define SW_PRESET2 sw_gpio_analog_2
#define SW_PRESET3 sw_gpio_analog_3
#define SW_CUT sw_gpio_33
#define SW_AUTO_CUT sw_gpio_32
//#define ? sw_gpio_34
//note: actual objects are created in global.cpp




//=============================
//======= configuration =======
//=============================
//--------------------------
//----- display config -----
//--------------------------
#if ESP_IDF_VERSION < ESP_IDF_VERSION_VAL(4, 0, 0)
#define HOST    HSPI_HOST
#else
#define HOST    SPI2_HOST
#endif
#define DISPLAY_PIN_NUM_MOSI GPIO_NUM_23
#define DISPLAY_PIN_NUM_CLK GPIO_NUM_22
#define DISPLAY_PIN_NUM_CS GPIO_NUM_27
#define DISPLAY_DELAY 2000
#define DISPLAY_BRIGHTNESS 8

//--------------------------
//----- encoder config -----
//--------------------------
#define ROT_ENC_A_GPIO GPIO_NUM_19
#define ROT_ENC_B_GPIO GPIO_NUM_21
#define ENABLE_HALF_STEPS false  // Set to true to enable tracking of rotary encoder at half step resolution
#define FLIP_DIRECTION    false  // Set to true to reverse the clockwise/counterclockwise sense



//--------------------------
//----- stepper config -----
//--------------------------
//enable stepper test mode (dont start control and encoder task)
//#define STEPPER_TEST
//pins
#define STEPPER_STEP_PIN		GPIO_NUM_18    //mos1
#define STEPPER_DIR_PIN			GPIO_NUM_16     //ST3
//driver settings
#define STEPPER_STEPS_PER_MM	(200/2)	//steps/mm (steps-per-rot / spindle-slope)
#define STEPPER_SPEED_DEFAULT	25		//mm/s
#define STEPPER_SPEED_MIN		4		//mm/s  - speed threshold at which stepper immediately starts/stops
#define STEPPER_ACCEL_INC		3		//steps/s increment per cycle 
#define STEPPER_DECEL_INC		7		//steps/s decrement per cycle
//options affecting movement are currently defined in guide-stepper.cpp


//---------------------------
//------- cable guide -------
//---------------------------
// default axis coordinates the guide changes direction (winding width)
#define GUIDE_MIN_MM 0  // TODO add feature so guide stays at zero for some steps (negative MIN_MM?), currently seems appropriate for even winding
#define GUIDE_MAX_MM 90 // 95 still to long at max pos - actual reel is 110, but currently guide turned out to stay at max position for too long, due to cable running diagonal from guide to reel

// tolerance added to last stored position at previous shutdown.
// When calibrating at startup the stepper moves for that sum to get track of zero position (ensure crashes into hardware limit for at least some time)
#define AUTO_HOME_TRAVEL_ADD_TO_LAST_POS_MM 20
#define MAX_TOTAL_AXIS_TRAVEL_MM 103 // max possible travel distance, needed as fallback for auto-home
#define LAYER_THICKNESS_MM 5         // height of one cable layer on reel -> increase in radius every layer
#define D_CABLE 6                    // determines winds per layer / guide speed
#define D_REEL 160                   // start diameter of empty reel

// max winding width that can be set using potentiometer (SET+PRESET1 buttons)
#define MAX_SELECTABLE_WINDING_WIDTH_MM 100;
// max target length that can be selected using potentiometer (SET button)
#define MAX_SELECTABLE_LENGTH_POTI_MM 100000
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

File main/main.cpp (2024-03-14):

extern "C"
{
#include <stdio.h>
#include <freertos/FreeRTOS.h>
#include <freertos/task.h>
#include <esp_idf_version.h>
#include "freertos/queue.h"
#include "esp_system.h"
#include "esp_log.h"
#include "driver/adc.h"

}

#include "config.h"
#include "global.hpp"
#include "control.hpp"
#include "buzzer.hpp"
#include "switchesAnalog.hpp"
#include "guide-stepper.hpp"
#include "encoder.hpp"
#include "shutdown.hpp"

#include "stepper.hpp"


//=================================
//=========== functions ===========
//=================================

//------------------------
//--- configure output ---
//------------------------
//configure a gpio pin as output
void gpio_configure_output(gpio_num_t gpio_pin){
    gpio_pad_select_gpio(gpio_pin);
    gpio_set_direction(gpio_pin, GPIO_MODE_OUTPUT);
}


//--------------------
//---- init gpios ----
//--------------------
void init_gpios(){
    //--- outputs ---
    //4x stepper mosfets
    gpio_configure_output(GPIO_VFD_FWD);
    gpio_configure_output(GPIO_VFD_D0);
    gpio_configure_output(GPIO_VFD_D1);
    gpio_configure_output(GPIO_VFD_REV);
    //gpio_configure_output(GPIO_VFD_D2); only used with 7.5kw vfd
    //2x power mosfets
    gpio_configure_output(GPIO_MOS1); //mos1
    gpio_configure_output(GPIO_LAMP); //llamp (mos2)
    //onboard relay and buzzer
    gpio_configure_output(GPIO_RELAY);
    gpio_configure_output(GPIO_BUZZER);
    //5v regulator
    gpio_configure_output(GPIO_NUM_17);

    //--- inputs ---
    //initialize and configure ADC
    adc1_config_width(ADC_WIDTH_BIT_12); //=> max resolution 4096
    adc1_config_channel_atten(ADC_CHANNEL_POTI, ADC_ATTEN_DB_11); //max voltage

    adc1_config_channel_atten(ADC_CHANNEL_SUPPLY_VOLTAGE, ADC_ATTEN_DB_11); //max voltage
}



//======================================
//============ buzzer task =============
//======================================
void task_buzzer( void * pvParameters ){
    ESP_LOGI("task_buzzer", "Start of buzzer task...");
        //run function that waits for a beep events to arrive in the queue
        //and processes them
        buzzer.processQueue();
}



//======================================
//=========== main function ============
//======================================
extern "C" void app_main()
{
    //init outputs and adc
    init_gpios();

    //enable 5V volage regulator (needed for display)
    gpio_set_level(GPIO_NUM_17, 1);

    //init encoder (global)
    encoder_queue = encoder_init();
    
    //define loglevel
    esp_log_level_set("*", ESP_LOG_INFO); //default loglevel
    esp_log_level_set("buzzer", ESP_LOG_ERROR);
    esp_log_level_set("switches-analog", ESP_LOG_WARN);
    esp_log_level_set("control", ESP_LOG_INFO);
    esp_log_level_set("stepper-driver", ESP_LOG_WARN);
    esp_log_level_set("stepper-ctrl", ESP_LOG_WARN);
    esp_log_level_set("Dendostepper", ESP_LOG_WARN); //stepper lib
    esp_log_level_set("calc", ESP_LOG_WARN); //stepper lib
    esp_log_level_set("lowVoltage", ESP_LOG_INFO);

#ifdef STEPPER_TEST
    //create task for testing the stepper motor
    xTaskCreate(task_stepper_test, "task_stepper_test", configMINIMAL_STACK_SIZE * 3, NULL, 2, NULL);
    //xTaskCreate(task_stepper_debug, "task_stepper_test", configMINIMAL_STACK_SIZE * 3, NULL, 2, NULL);
#else
    //create task for detecting power-off
    xTaskCreate(&task_shutDownDetection, "task_shutdownDet", 2048, NULL, 2, NULL);
    // wait for nvs to be initialized in shutDownDetection task
    vTaskDelay(50 / portTICK_PERIOD_MS);

    //create task for controlling the machine
    xTaskCreate(task_control, "task_control", configMINIMAL_STACK_SIZE * 3, NULL, 4, NULL);

    //create task for controlling the stepper motor (linear axis that guids the cable)
    xTaskCreate(task_stepper_ctl, "task_stepper_ctl", configMINIMAL_STACK_SIZE * 3, NULL, 2, NULL);
#endif

    //create task for handling the buzzer
    xTaskCreate(&task_buzzer, "task_buzzer", 2048, NULL, 2, NULL);

    //beep at startup
    buzzer.beep(3, 70, 50);
}

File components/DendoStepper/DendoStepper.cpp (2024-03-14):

#include "DendoStepper.h"
#include "esp_log.h"

#define STEP_DEBUG

#ifdef STEP_DEBUG
#define STEP_LOGI(...) ESP_LOGI(__VA_ARGS__)
#define STEP_LOGW(...) ESP_LOGW(__VA_ARGS__)
#define STEP_LOGE(...) ESP_LOGE(__VA_ARGS__)
#else
#define STEP_LOGI(...) while (0)
#define STEP_LOGW(...) while (0)
#define STEP_LOGE(...) ESP_LOGE(__VA_ARGS__)
#endif

bool state = 0;

// PUBLIC definitions

DendoStepper::DendoStepper()
{
}

void DendoStepper::config(DendoStepper_config_t *config)
{
    memcpy(&conf, config, sizeof(conf));
}

void DendoStepper::disableMotor()
{
    setEn(true);
    STEP_LOGI("DendoStepper", "Disabled");
    ctrl.status = DISABLED;
}

void DendoStepper::enableMotor()
{
    setEn(false);
    ctrl.status = IDLE;
    STEP_LOGI("DendoStepper", "Enabled");
    timerStarted = 0;
}

void DendoStepper::init(uint8_t stepP, uint8_t dirP, uint8_t enP, timer_group_t group, timer_idx_t index, microStepping_t microstepping = MICROSTEP_1, uint16_t stepsPerRot = 200)
{
    conf.stepPin = stepP;
    conf.dirPin = dirP;
    conf.enPin = enP;
    conf.timer_group = group;
    conf.timer_idx = index;
    conf.miStep = microstepping;
    ctrl.status = 0;
    init();
}

void DendoStepper::init()
{
    uint64_t mask = (1ULL << conf.stepPin) | (1ULL << conf.dirPin) | (1ULL << conf.enPin); // put output gpio pins in bitmask
    gpio_config_t gpio_conf = {
        // config gpios
        .pin_bit_mask = mask,
        .mode = GPIO_MODE_OUTPUT,
        .pull_up_en = GPIO_PULLUP_DISABLE,
        .pull_down_en = GPIO_PULLDOWN_DISABLE,
        .intr_type = GPIO_INTR_DISABLE,
    };
    // set the gpios as per gpio_conf
    ESP_ERROR_CHECK(gpio_config(&gpio_conf));

    timer_config_t timer_conf = {
        .alarm_en = TIMER_ALARM_EN,         // we need alarm
        .counter_en = TIMER_PAUSE,          // dont start now lol
        .intr_type = TIMER_INTR_LEVEL,      // interrupt
        .counter_dir = TIMER_COUNT_UP,      // count up duh
        .auto_reload = TIMER_AUTORELOAD_EN, // reload pls
        .divider = 80000000ULL / TIMER_F,   // ns resolution
    };

    // calculate stepsPerRot
    ctrl.stepsPerRot = (360.0 / conf.stepAngle) * conf.miStep;

    STEP_LOGI("DendoStepper", "Steps per one rotation:%d", ctrl.stepsPerRot);

    if (conf.timer_group != TIMER_GROUP_MAX && conf.timer_idx != TIMER_MAX)
    {
        // timer was configured explixitly in config structure, we dont need to do it here
        goto timer_avail;
    }

    // try to find free timer
    timer_config_t temp;
    for (int i = 0; i < 1; i++)
    {
        for (int j = 0; j < 1; j++)
        {
            timer_get_config((timer_group_t)i, (timer_idx_t)j, &temp);
            if (temp.alarm_en == TIMER_ALARM_DIS)
            {
                // if the alarm is disabled, chances are no other dendostepper instance is using it
                conf.timer_group = (timer_group_t)i;
                conf.timer_idx = (timer_idx_t)j;
                goto timer_avail;
            }
        }
    }

    // if we got here it means that there isnt any free timer available
    STEP_LOGE("DendoStepper", "No free timer available, this stepper wont work");
    return;

timer_avail:
    ESP_ERROR_CHECK(timer_init(conf.timer_group, conf.timer_idx, &timer_conf));                   // init the timer
    ESP_ERROR_CHECK(timer_set_counter_value(conf.timer_group, conf.timer_idx, 0));                // set it to 0
    ESP_ERROR_CHECK(timer_isr_callback_add(conf.timer_group, conf.timer_idx, xISRwrap, this, 0)); // add callback fn to run when alarm is triggrd
}

esp_err_t DendoStepper::runPos(int32_t relative)
{
    //TODO only enable when actually moving
    if (ctrl.status == DISABLED) // if motor is disabled, enable it
        enableMotor();

    if (!relative) // why would u call it with 0 wtf
        return ESP_ERR_NOT_SUPPORTED;

    if (ctrl.status > IDLE) { //currently moving
        bool newDir = (relative < 0); // CCW if <0, else set CW
        if (ctrl.dir == newDir){ //current direction is the same
            ctrl.statusPrev = ctrl.status; //update previous status
            ctrl.status = ctrl.status==COAST ? COAST : ACC; //stay at coast otherwise switch to ACC
            calc(abs(relative + ctrl.stepsRemaining)); //calculate new velolcity profile for new+remaining steps
        } else { //direction has changed
                 //direction change not supported TODO wait for decel finish / queue?
            STEP_LOGW("DendoStepper", "DIRECTION HOT-CHANGE NOT SUPPORTED - Finising previous move, this command will be ignored");
            return ESP_ERR_NOT_SUPPORTED;
        }
    }
    else { //current state is IDLE
        ctrl.statusPrev = ctrl.status; //update previous status
        ctrl.status = ACC;
        setDir(relative < 0); // set CCW if <0, else set CW
        calc(abs(relative));                                                                         // calculate velocity profile
    }

    currentPos += relative; //(target position / not actual)
    ESP_ERROR_CHECK(timer_set_alarm_value(conf.timer_group, conf.timer_idx, ctrl.stepInterval)); // set HW timer alarm to stepinterval
                                                                                                 //TODO timer has to be stopped before update if already running?
    ESP_ERROR_CHECK(timer_start(conf.timer_group, conf.timer_idx));                              // start the timer

    return ESP_OK;
}

esp_err_t DendoStepper::runPosMm(int32_t relative)
{
    if (ctrl.stepsPerMm == 0)
    {
        STEP_LOGE("DendoStepper", "Steps per millimeter not set, cannot move!");
    }
    return runPos(relative * ctrl.stepsPerMm);
}

esp_err_t DendoStepper::runAbs(uint32_t position)
{
    if (getState() > IDLE) // we are already moving, so stop it
        stop();
    while (getState() > IDLE)
    {
        // waiting for idle, watchdog should take care of inf loop if it occurs
        vTaskDelay(1);
    } // shouldnt take long tho

    if (position == currentPos) // we cant go anywhere
        return 0;

    int32_t relativeSteps = 0;
    relativeSteps = (int32_t)position - currentPos;

    ESP_LOGI("DendoStepper", "Cur: %llu move %d", currentPos, relativeSteps);
    return runPos(relativeSteps); // run to new position
}

esp_err_t DendoStepper::runAbsMm(uint32_t position)
{
    if (ctrl.stepsPerMm == 0)
    {
        STEP_LOGE("DendoStepper", "Steps per millimeter not set, cannot move!");
    }
    return runAbs(position * ctrl.stepsPerMm);
}

void DendoStepper::setSpeed(uint32_t speed, uint16_t accT, uint16_t decT)
{
    ctrl.speed = speed;
    ctrl.acc = ctrl.speed / (accT / 4000.0);
    ctrl.dec = ctrl.speed / (decT / 4000.0);
    STEP_LOGI("DendoStepper", "Speed set: %d steps/s t+=%d s t-=%d s", speed, accT, decT);
}
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

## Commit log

2022-08-06 init - display test
    new idf project (with idf.py create-project)
    add 2 components for encoder and display:
    https://github.com/DavidAntliff/esp32-rotary-encoder
    https://github.com/UncleRus/esp-idf-lib/tree/master/components/max7219
    add code for testing a 7 segment display
2022-08-07 Add rotary encoder test
    for testing the rotary encoder the count is displayed on the 7 segment display
    (1 rotation = 600)
2022-08-17 Add config, buzzer, evalSwitch, switch to c++
    Add config.cpp/hpp
    - macros for all input and output pins
    - gloabl evaluated switch objects
    - buzzer object
    - display config
    - encoder config
    Move main.c to main.cpp and adjust code to be c++ compatible
    add custom library evaluated switch (copied from armchair project)
    add buzzer object (copied from armchair project)
    add control.cpp/hpp with control task (no function yet)
    [buzzer.cpp, config.cpp, config.hpp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]
2022-08-17 Add Readme, connection-plan, function-diagram
    Readme:
    - component description
    connection plan:
    - fully connected pcb
    - control panel overview with all input elements
    function-diagram:
    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
2022-08-17 Move code from main to control.cpp, display pages
    - move code from testing task to control.cpp
    - outsource functions for initializing display and encoder
    - delete testing code
    - add two display pages (current distance and counter)
    - run handle functions for each button
2022-08-17 Add vfd driver, Add vfd test via buttons
    Add vfd.cpp/hpp with functions to control the VFD via 4 digital pins
    Add way to test the vfd via SET button (rotate speed level) and START
    button (toggle motor on/off)
2022-08-17 Swap vfd data pins, Update connection plan
    Tested new vfd functions, encoder and display - works as intended now
    [vfd.cpp]
2022-08-18 Update function-diagram: SM, Buttons, Display
    Create function diagram with all currently planned features
2022-08-18 Add poti and display section; Cleanup
    Add readadc function from armchair project
    Rework display section
    - show lengthNow on first display
    - show lengthTarget on second display
    Prepare for statemachine
    Remove unneeded function
    Add comments improve structure
    [config.hpp, control.cpp, main.cpp]
2022-08-18 Fix disabled encoder, scaling; Adjust intervals
    test with actual hardware
    encoder init was commented out
    scaling was off by factor 600
    adjust speed intervals
    [control.cpp]
2022-08-18 Update connection-plan, function-diagram
    function diagram represents currently implemented control
    - add vfd reverse
    - optimizations, fixes
    - wire colors
    - 7 segment display wiring
    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
2022-08-19 Add MANUAL mode, Add vfd direction support
    vfd: extend vfd_setState function with direction enum (default fwd)
    main: reduce log output from buzzer task
    config: use mos1 as vfd_FWD output
    control:
    add MANUAL state: motor can be controlled via preset buttons
    adjust code slightly to support new state (also see updated
    function-diagram)
    [config.hpp, control.cpp, main.cpp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]
2022-08-20 Change/Add sw pulldown resistors, Fix MANUAL mode
    Analog In only pins have no internal pullup resistors.
    thus two preset switches need pulldown resistors on pcb to be soldered
    and switch to 3v instead of GND
    - changed in connection plan
    - changed switch config in config.cpp (no pullup, inverted)
    Fix manual mode:
    previously there was a bugged change loop when pressing all 3 buttons
    - made mode switch more clear
    [config.cpp, control.cpp]
2022-08-20 Fix bugs MANUAL mode, Adjustments new VFD
    fix bugs introduced with addition of manual mode:
    - fix stuck in target_reached state
    - fix bug switch to manual mode only in counting possible
    new vfd
    - new 750W vfd has 1 speed select pin less -> limit used
    levels to 0-3
    [control.cpp]
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2022-08-20 Add preset buttons; Optimizations
    - add functionality to set preset lengths with preset buttons
    - change variables
    - add/change comments
    - reorder code
    - add beeping at custom length selection
2022-08-20 Add dyn-speed to start state; Update function-diagram
    - outsource dynamic speed to setDynSpeedLvl function
    - reuse function in wind-slow state with limit
    - update function diagram to representation of current program
2022-08-21 Fix bug custom length, add hyst; Adjust beeping
    - Fix bug where custom length did not get rounded
    - Reduce beeping lengths, remove gap between beep events
    - Add hysteresis to custom length selection to prevent unwanted beeps or
    flickering display at certain poti positions
    - change max loglevel to verbose in menuconfig
    [buzzer.cpp, config.cpp, control.cpp]
2022-08-21 Fix bug spi init; Fix random string + flickering
    Fix bug where sartup randomly crasehd several times because spi config
    was initialized with random data -> init with 0
    Fix bug where length now was not truncated resulting in flickerin
    Fix bug in welcome message where hello string contained random data
    [control.cpp, display.cpp]
2022-08-21 Add blink strings functionality
    add functions to display.cpp
    - void display2_handle();
    - void display2_blinkStrings(const char * strOn, const char * strOff, uint32_t msOn, uint32_t msOff);
    control.cpp:
    - blink target length when set button is pressed
    - blink MANUAL when in manual mode
2022-08-22 Show manual speed lvl; Change buf
    - when in manual mode blink between 'manual' and motor 'lvl' on bottom
    display
    - optimize buffer variables and sizes
2022-08-22 Revert "Show manual speed lvl; Change buf"
    This reverts commit 4e2cc070d1200164f652e07ca513fe0de1873ed3.
    Other approach for displaying manual speed lvl found
    [control.cpp]
2022-08-23 Disp: show manual lvl and dir, brightness, soll blink
    - in manual mode blink between 'manual' and lvl+direction indication on
    display 2
    - when setting custom target length only blink value not "soll"
    - reduce brightness from 12 to 8 because of high display temperature
2022-08-23 Add blink method to display class
    - Add method to trigger blinking of the display for a certain count and durations
    also with a optional off-string
    - Add 3x blinking after applying a new target length with preset or set
    buttons
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2022-09-06 Fix random cutter stops (evaluateSwitch)
    - use evaluatedSwitch class for position switch instead of reading gpio
    directly because it triggered incorrectly too often
    - cutter_stop() only switch to CANCELED when not in IDLE already
    [cutter.cpp, main.cpp]
2022-09-11 Add schematic, layout, calculations for 4swToAdc
    Add details and calculations for a stripboard with a resistor network that makes it
    possible to connect 4 switches (to gnd) to one adc pin of the controller
    [4swToAdc.kicad_sch, 4swToAdc_stripboard-calc.ods]
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2022-09-12 EvalSwitch: Add func as source, remove dupl code
    evaluatedSwitch component:
    - remove duplicate code for inverted and non-inverted mode
    - add new constructor for instance with a function to obtain current
    input state instead of gpio pin (e.g. needed for 4switches on analog input)
    [gpio_evaluateSwitch.cpp]
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2022-09-12 Rework switch-assignment, Update connection-plan
    Rework config.cpp and config.hpp:
    - different naming convention for evaluated switch objects
    - thus updated macros for switches
    - add new evalswitch instances for 4 switches on 1 adc
    - update switch assignment, use the 4 new inputs
    Update connection plan with new assignment, add stripboard details
    [config.cpp, config.hpp, main.cpp]
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2022-09-15 Update connection plan: New Control-panel layout
    Replace previous control panel with to scale svg exported from cad with
    button descriptions
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2022-09-19 Add delay to auto-cut, beep countdown
    Add 3s delay between target reached and automatic cut
    During that delay the buzzer keeps beeping faster until the cut starts.
    [control.cpp]
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2022-09-19 Fix display priority, Add stop countdown
    Fix bug where display is stuck when countdown stopped via reset button
    Add functionality to stop countdown via turning auto-cut switch off
    Fix display priority issues with using 2 boolean variables and a delay
    before counting
    [control.cpp]
2022-09-19 Add cutter stop via btn; Prevent cut while winding
    Add conditions to CUT button pressed case
    - when cutter already on -> stop
    - when in state where motor is active -> dont start
    - else: error
    [control.cpp]
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2022-09-22 Add basic LAMP functionality; Fix comments
    - Basic lamp functionality: simply turn on when not in COUNTING or TARGET_REACHED
    state
    - Remove unnecessary comments, fix code formatting in several files
    [control.cpp, cutter.cpp, main.cpp]
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2022-09-23 Add blinking at RESET; Adjust preset values
    Blink 'IST' value on top display when reset (as with presets)
    Adjust preset values to current labeling
    [control.cpp]
2022-09-29 Add autoCut-cancel with any button; Fix display init
    - Pending auto cut (countdown) can be canceled using any button on the
    panel
    - Reset button does not reset the length when countdown cancledo
    - Fix bug where display did not initialize correctly after start some
    times
    -> simply init again after welcome msg
    - reduce countdown time by 500ms
    [control.cpp, display.cpp]
2022-09-29 Add CAD-files, wire-labels, docs/datasheets
    Add add cad files of all designed and 3d-printed parts.
    Mostly Freecad and a few older SolidEdge files (_SE)
    Add wire-labels.fods containing the printed labels for wires in
    control-box and switching cabinet
    Add docs folder with relevant images and datasheets of the used components
    [angle-bracket_v2.0.FCStd, box-holder_v1.0.FCStd, box_v1.0.FCStd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]
2022-09-30 Add LENGTH_OFFSET and REACHED_TOLERANCE options
    Add feature and config option #define TARGET_LENGTH_OFFSET
    that makes it possible to set a distance that gets added to the target
    length, thus preventing falling short on the actual length when spools
    rotates back slightly after stop.
    Also move reached tolerance to config.
    [config.hpp, control.cpp]
2022-10-13 Update diagram pdf files, cad files (guides)
    - update / export pdf version from current drawio connection-plan and
    function-diagram
    - update cad files
    [guide-cutter_v5.1.FCStd, guide-in_v2.1.FCStd]
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2023-02-21 Add cad file (axis mounts)
    This file currently contains
    - crude model of linear-axis
    - angled bracket for mounting the axis to item
    - 2 versions of interface between rolls and axis
    - rolls
    [axis_mounts.FCStd]
2023-02-22 Fix include order for compatibility
    including the files in source file instead of header file fixed
    'conflicting type' errors in idf macros when using newer version
    ESP-IDF v4.4.4-148-g4c2afac355
    [guide-stepper.cpp]
2023-02-27 Adjust test-params, CAD: enforce axis-mount
    While testing the setup
    Optimizations of problems noticed while testing the setup:
    - mount too weak
    - only very slow speeds relevant
    - less distance required
    [axis-mount.stl, axis_mounts.FCStd]
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2023-03-01 Fix variable scopes (static), Simplify encoder
    - add static type to all local variables in every source file
    so the scope of each variable is limited to that file.
    This prevents conflicting variable names with other source file
    (e.g. 'state' variable in vfd.cpp)
    - simplify encoder concept
    wrap all used functions from rotary_encoder.h library in
    custom encoder.hpp file
    -> only one file has to be included where encoder is used
    -> global variable 'encoder' is not necessary anymore
    -> reduces duplicate code for length calculation
    - update all files where encoder functions where used accordingly
    [control.cpp, cutter.cpp, encoder.cpp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]
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2023-03-01 Swap VFD and Stepper pin, Swap Encoder connection
    - update config and connection plan
    - swap B+ and B- of encoder to invert the rotational direction,
    so the direction in code make more sense
    - swap VFD and stepper pin. For some reason stepper did not work with
    dir pin on mos2. Maybe pulse affected dir pin, try again with denoise
    pcb
    [config.hpp]
2023-03-01 Fix rounding, Rework step-calc, Tested
    - decrease home speed
    - invert direction in stepper test and home function due to changed
    wiring
    - stretch travel steps calculation to multiple steps and variables for
    better overview and debugging
    - prevent partial steps from being lost -> fixes rounding issue
    TESTED: works in general, but steper movement is too jerky. Also there
    is a Hardware issue: When VFD/motor is on the steper does not work
    properly -> 50ohm pullup near stepper driver fixed this
    [guide-stepper.cpp, main.cpp]
2023-03-02 Add filter-pcb for denoising stepper signals
    When the VFD was running the stepper driver did not work correctly.
    The especially the DIR signal got unusable and triggered randomly.
    Add custom stripboard that reduces the noise on DIR and PULSE data
    lines.
    The circuit simply increases the current in the data lines significantly
    and crops the voltage to 0-5V using a zener diode.
    While testing with an oscilloscope the circuit seems effective.
    - add kicad schematic
    - add spreadsheet with stripboard layout
    - update connection: plan with stripboard, update changed 5V connection
    [4swToAdc.kicad_sch, 4swToAdc_stripboard-calc.ods, filter_stripboard.ods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]
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2023-03-13 Stepper: add mutex, logging, delay, less steps
    When testing last commit the stepper task crashed almost instantly and
    moved randomly. Trying to fix/debug that with those changes
    [DendoStepper.cpp, DendoStepper.h, guide-stepper.cpp]
2023-03-13 revert mutex, fix state reset, logging, slower
    stepsRemaining not necessary in ISR
    comment out forced stop at runAbs
    statusPrev not needed
    TODO: ISR defines state every time, no need to adjust manually while running
    adjust calc function to handle remaining steps
    Test: broken - slow moves mork but when "extending" movement it just
    vibrates
    [DendoStepper.cpp, guide-stepper.cpp, main.cpp]
2023-03-13 Stepper: rework resume functionality
    [DendoStepper.cpp, guide-stepper.cpp]
2023-03-13 Stepper: Add calc debug output ISSUES
    - sometimes deadlock at direction change
    waits for idle state in runAbs
    function, but stepper is not really moving anymore ISR does not change
    to idle or state changed afterwards?
    - every EXTEND operation results in a motor stop thus when extending
    alot is stopped only ramping up and down
    when encoder stop after several extend attempts
    the stepper moves all the remaining steps successfully
    [DendoStepper.cpp]
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2023-03-24 Fix feature: extend movement works now! (test mode)
    while currently in stepper test mode the extend feature works as
    intended now.
    you can trigger movement using the buttons and repeating
    presses while still moving (coast, accel or decel) extends the movement
    without stopping or accelerating again.
    Note reversing the direction while still moving is not handled and results
    in immediate direction change and distance that makes no sense.
    also added alot of debug output and switched to debug level
    [DendoStepper.cpp, guide-stepper.cpp, main.cpp]
2023-03-26 Add more debug output ISSUES
    - Add debug output in calc
    - disable test mode for testing with encoder
    - set loglevel to DEBUG
    extend feature currently only works well in testing mode with buttons
    issues when running with encoder:
    movement gets extended extremely often due to encoder travel
    interval and rarely does reach target - compared to trigger with
    -> while debugging noticed that the current speed gets negative
    and the xISR gets stuck so moves infinitely or not at all
    ideas:
    - rounding issue?
    - SPEED increment also has to be adjusted or set to 0 as step
    increment?
    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
    [DendoStepper.cpp, config.hpp, guide-stepper.cpp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]
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2023-04-11 Fixes, Works but crashes when finished accelerating
    Some adjustments to make it work
    - fix direction change (temporary)
    - fix isr initial start
    See notes in stepper.cpp
    Todo:
    - fix crash after accelerating
    - add initial speed (takes long to accelerate from 0
    -
    [guide-stepper.cpp, stepper.cpp]
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2023-04-24 New implementation with timer, partial functional (WIP)
    Partially implemented stepper driver as planned in diagram
    works partially (reset button toggles distances)
    major issues though - wip
    needs debugging and testing
    [guide-stepper.cpp, main.cpp, stepper.cpp]
2023-04-25 Remove unused code, potential bugfix
    remove commented out code and unused code from previous approach
    addition al check that might fix issue with underflow
    [guide-stepper.cpp, stepper.cpp]
2023-04-25 Fix isr-function (fully functional now), Add task for debug output
    new driver works well while testing with one button with debug output
    - small changes to isr function that made it fully functional!
    - add stepper debug task
    - minor optimizations necessary
    [guide-stepper.cpp, main.cpp, stepper.cpp]
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2023-04-25 Revert 8 commits (approach with stepper lib dropped)
    Undo all custom changes to the DendoStepper library, since it will not
    be used further. Custom implementation will be used in the future
    (stepper_custom-driver branch)
    Revert 279ac0e07e7578a86a6d13908e472bd4f379a62a
    Revert 1c59e0097b3732d9b035881faa442349c50d4341
    Revert 5d7c67ab9a2327adc49ea92cd55f9aa23a40b065
    Revert 8d2428d28576e08da07af79659620376b1e4e964
    Revert dc6deeb3d09628ac7f4f4fab256dc168bcbf835a
    Revert 0a05340763c26be4735d1cf845b96150112b25ad
    Revert 45409676a0b502c69b5bc26be7361bfa5a89ed61
    Revert de42b6252ebec3558713cd39334548041654545f
    [DendoStepper.cpp, DendoStepper.h, guide-stepper.cpp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]
2023-04-26 Move stepper-cfg to config.h, Rework guide-stepper.cpp (new driver)
    - move stepper config e.g. speed accel steps... from stepper.cpp to
    config.h
    - uncomment and rework code in guide-stepper.cpp (for traveling the
    stepper based on encoder) to work with new custom driver instead of
    previous library
    Note currently in STEPPER_SIMULATE_ECNODER mode (use button as encoder),
    see macro
    [config.hpp, guide-stepper.cpp, stepper.cpp]
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2023-04-28 Stepper driver: Add overshoot
    - prevent hard stops (no decel ramp) when target changes while
    decelerating already (overshoot and move back)
    - optimize/adjust stepper-test mode, add macro for test with single switch
    Note: tested the current state, works quite well. very rarely crashes
    probably dude to race conditions in isr?
    [config.hpp, guide-stepper.cpp, stepper.cpp]
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2023-11-29 CAD: Add reel_v2.2 with interlocking counter-part
    - Add new version of cable reel with second counter-part
    to prevent cable from falling off at long lengths
    - Also update axis-mounts (modified some time ago)
    [axis_mounts.FCStd, cable-reel_v2.2.FCStd]
2023-12-11 CAD: Update reel v2.2 (printed)
    - slight adjustments to parameters
    -> printed this version in PETG
    [cable-reel_v2.2.FCStd]
2024-03-08 Fix Bug 'weird axis movement at reset'
    - guide-stepper:
    - add queue to send commands to stepper-ctl task
    - add function that tells stepper task to move to zero
    - increase travel length full axis length 110
    - control: move guide to zero at reset
    - Cmake: enable colored output
    [control.cpp, guide-stepper.cpp, main.cpp]
2024-03-09 Add layer-count, variable diameter, Optimize comments
    guide-stepper:
    - Add layer count when reversing axis
    - Adjust steps calculation considering (add layers to reel-dia)
    - optimize comments
    control: optimize comments
    main: optimize comments
    [config.hpp, control.cpp, guide-stepper.cpp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]
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2024-03-10 Outsource global variables, Optimize comments
    - outsource global variables and objects
    - move from config.hpp to global.cpp / hpp
    - rename config.hpp, thus change all includes
    - re-arrange includes -> in source files instead of header
    - optimize / make function comment titles more consistent
    - optimize comments overall
    - add several temporary files to gitignore
    - fix unused variable compiler warnings
    [buzzer.cpp, config.h, control.cpp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]
2024-03-11 CAD: Add cable-reel_v2.2.2, Update axis_mounts
    Currently used sturdier version of cable reel with
    attachable counter piece, printed using PETG
    Currently used Axis components:
    Changed rolls and mount block
    Details see changelog in FCStd files (param spreadsheet)
    [axis_mounts.FCStd, cable-reel_v2.2.2.FCStd]
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2024-03-13 Fix ENCODER_TEST, Calibrate length measurement
    config:
    - calibrate length measurement
    - Fix ENCODER_TEST
    - syntax error
    - Add beep at 0.5m
    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
    [config.h, control.cpp]
2024-03-13 Update Connection-plan: Measure voltage, Details, Color
    connection-plan:
    - Add supply voltage measurement (onboard)
    - re-wire blue led
    - add github link
    - optimize panel description
    - add stepper information, fix color
    - wiring plan: Add specifications, Add colorconnection-plan:
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2024-03-16 Fix deadlock in windingWidth, Handle 0 width, optimize UI
    - fix deadlock when editing winding width
    - fix behaivor when windingWidth is set to 0 (disable guide)
    - add dead time to prevent setTarget when exiting setWindingWidth with buttons
    - fix typo and conditons
    - increase max winding width
    - optimize display text
    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
    [config.h, control.cpp, guide-stepper.cpp]
2024-03-17 Add dynamic-winding-length depending on targetLength
    When winding short lengths e.g. 5m it does not make sense
    to use the entire winding width thus getting unnecessary
    wide cable ring.
    Determined some thresholds while testing and implemented
    those to be applied at target length change automatically:
    - update winding width each time target length changes
    - add function that returns dynamic winding width depending
    on passed target length according to fixed thresholds
    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
    [config.h, control.cpp, guide-stepper.cpp]
2024-03-23 CAD: Add assembly of all parts (for website)
    Due to color changes of linked parts all files got changed
    (meaning no actual modifications to parts was made)
    [angle-bracket_v2.0.FCStd, assembly_all-parts.FCStd, axis_mounts.FCStd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]
